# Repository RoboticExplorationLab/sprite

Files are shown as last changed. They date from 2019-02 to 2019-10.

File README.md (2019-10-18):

[hardware](https://github.com/maholli/sprite/tree/master/hardware): KiCad PCB files and bill of materials. Assembling a sprite? Check out [https://roboticexplorationlab.github.io/sprite/](https://roboticexplorationlab.github.io/sprite/) for an interactive BOM!

[firmware](https://github.com/maholli/sprite/tree/master/firmware): pre-built circuitpython bootloader.bin and firmware.uf2 (and the files to build it yourself)

[software](https://github.com/maholli/sprite/tree/master/software): circuitpython scripts and libraries working on the sprite

<br>
<br>
<br>

----

<p align="middle">
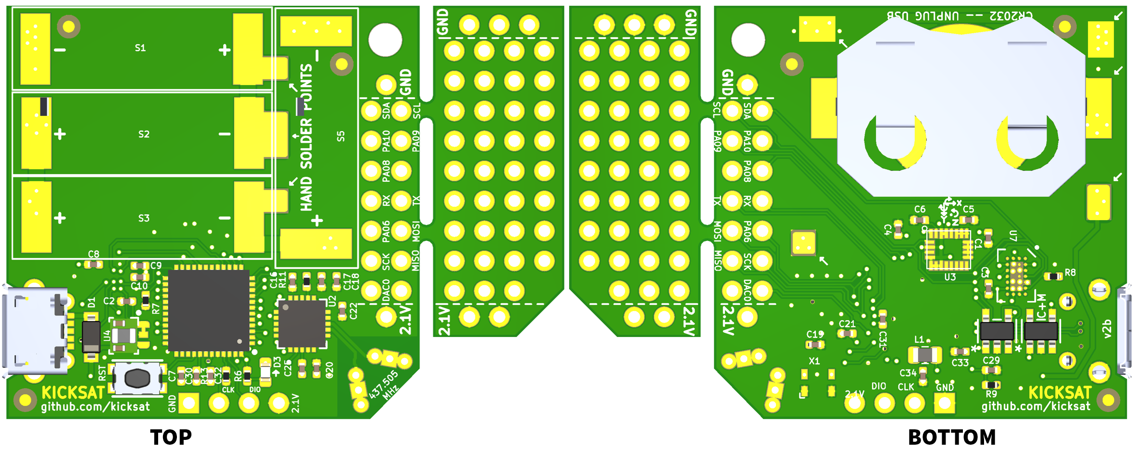
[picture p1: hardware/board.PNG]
  
</p>

### 💡 Lots of applicable information also located on the [PyCubed.org quickstart page](https://www.notion.so/maholli/Hands-On-Quick-Start-d220f0ec88eb41c08ee855ff4f46d737).

## Demos

Put all the files located in [/software/](/software/) on to the sprite and start the serial console (as described above). After pressing <kbd>Ctrl</kbd>+<kbd>C</kbd> to halt the sprite, press any key to enter the REPL, then type

```
import NAMEOFFILE
```

and press enter to execute the example. For example, it we wanted to run blink.py, it would be...

```
import blink
```

1. blink.py - will blink the green LED. 
2. i2c_IMU.py - samples all available sensors on the IMU and prints the results
3. cursor.py - uses the X,Y data from the IMU accelerometer and moves the computer cursor accordingly
4. cpc_test.py - example transmit message for the CC1101 radio

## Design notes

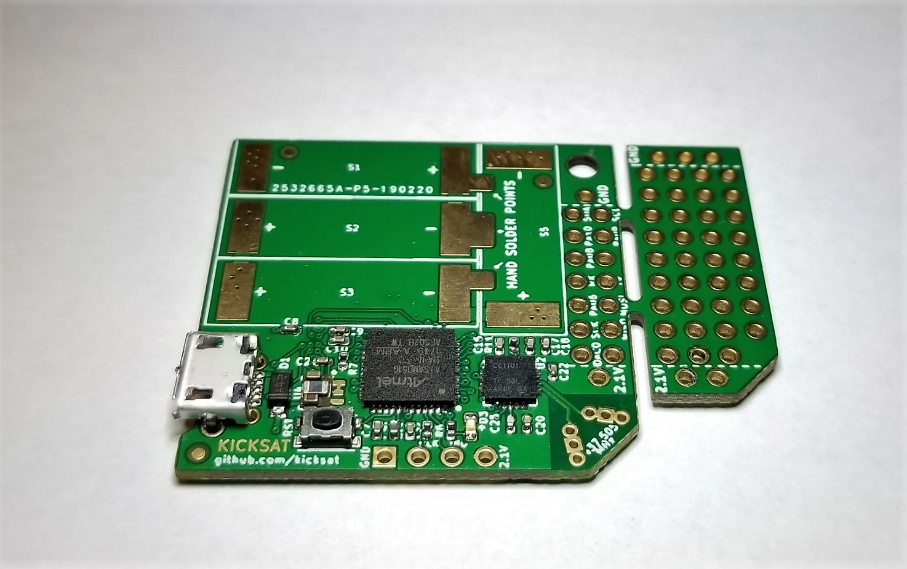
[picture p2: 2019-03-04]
hardware/sprite_top.jpg

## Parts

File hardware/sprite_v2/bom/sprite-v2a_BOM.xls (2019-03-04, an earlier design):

BOM: sprite-v2a
Assembly Part Number/Revision: v2a
Customer / Company Name: Max Holliday, Stanford University
Item # | Quantity per board | Manufacturer Part # | Do Not Install | Reference designators | Vendor (optional) | Vendor Part Number (optional) | Value (optional) | Size / Footprint (optional) | Part description/ specs (optional, but recommended) | Manfacturer (optional)
2 | 1 | 7L2609LCSC-CGG4S |  | X1 |  |  | 26.000 |  | TXCO_2.5x2
3 | 1 | CC1101RGPR |  | U2 |  |  | CC1101RGPR |  | CC1101_RGP_20
4 | 1 | OVM9724 | DNI | U7 |  |  | OVM9724 |  | OVM9724b
5 | 1 | BAT-HLD-001 | DNI | U1 |  |  | BAT-HLD-001 |  | BAT-HLD-001
10 | 1 | 10118194-0001LF |  | J1 |  |  | 10118194-0001LF |  | 10118194-0001LF
11 | 1 | CMI201209X100KT |  | L1 |  |  | 10uH |  | L_0805_2012Metric
12 | 4 | CL05B105KQ5NQNC |  | C7,C29,C33,C31 |  |  | 1uF |  | C_0402_1005Metric
14 | 1 | SOD4004-SH |  | D1 |  |  | MBR120 |  | D_SOD-123
15 | 1 | TJ-S1608SW6TGLC2G-A5 |  | D3 |  |  | GREEN LED |  | LED_0603_1608Metric
16 | 4 | KXOB22-04X3F | DNI | S3,S5,S1,S2 |  |  | KXOB22-04X3F |  | KXOB22-12X1F
17 | 1 | TPS82740ASIP |  | U4 |  |  | TPS82740ASIP |  | TPS82740ASIPR
18 | 4 | RTT021002FTH |  | R8,R9,R13,R7 |  |  | 10K |  | R_0402_1005Metric
19 | 1 | ATSAMD51G_TQFN48 |  | U6 |  |  | ATSAMD51G_TQFN48 |  | QFN50P700X700X90-49N-D
21 | 3 | 0402X106M6R3NT |  | C30,C34,C1 |  |  | 10uF |  | C_0402_1005Metric
22 | 10 | CL05B104KO5NNNC |  | C32,C10,C9,C8,C3,C2,C6,C4,C22,C21 |  |  | 0.1uF |  | C_0402_1005Metric
23 | 2 | DS90LV012ATMFX/NOPB | DNI | U9,U8 |  |  | DS90LV012ATMFX_NOPB |  | DS90
25 | 1 | KMR631NGULCLFS |  | SW2 |  |  | KMR231NG LFS |  | BTN_KMR2_4.6X2.8
26 | 1 | RC0402FR-0756KL |  | R11 |  |  | 56K |  | R_0402_1005Metric
27 | 1 | RC0402FR-07330RL |  | R6 |  |  | 330 |  | R_0402_1005Metric
28 | 4 | CC0402JRX7R9BB103 |  | C25,C20,C18,C5 |  |  | 10nF |  | C_0402_1005Metric
30 | 3 | 0402B221K500NT |  | C19,C17,C16 |  |  | 220pF |  | C_0402_1005Metric
31 | 1 | LSM9DS1TR |  | U3 |  |  | LSM9DS1 |  | LGA24-8X4
END OF BOM

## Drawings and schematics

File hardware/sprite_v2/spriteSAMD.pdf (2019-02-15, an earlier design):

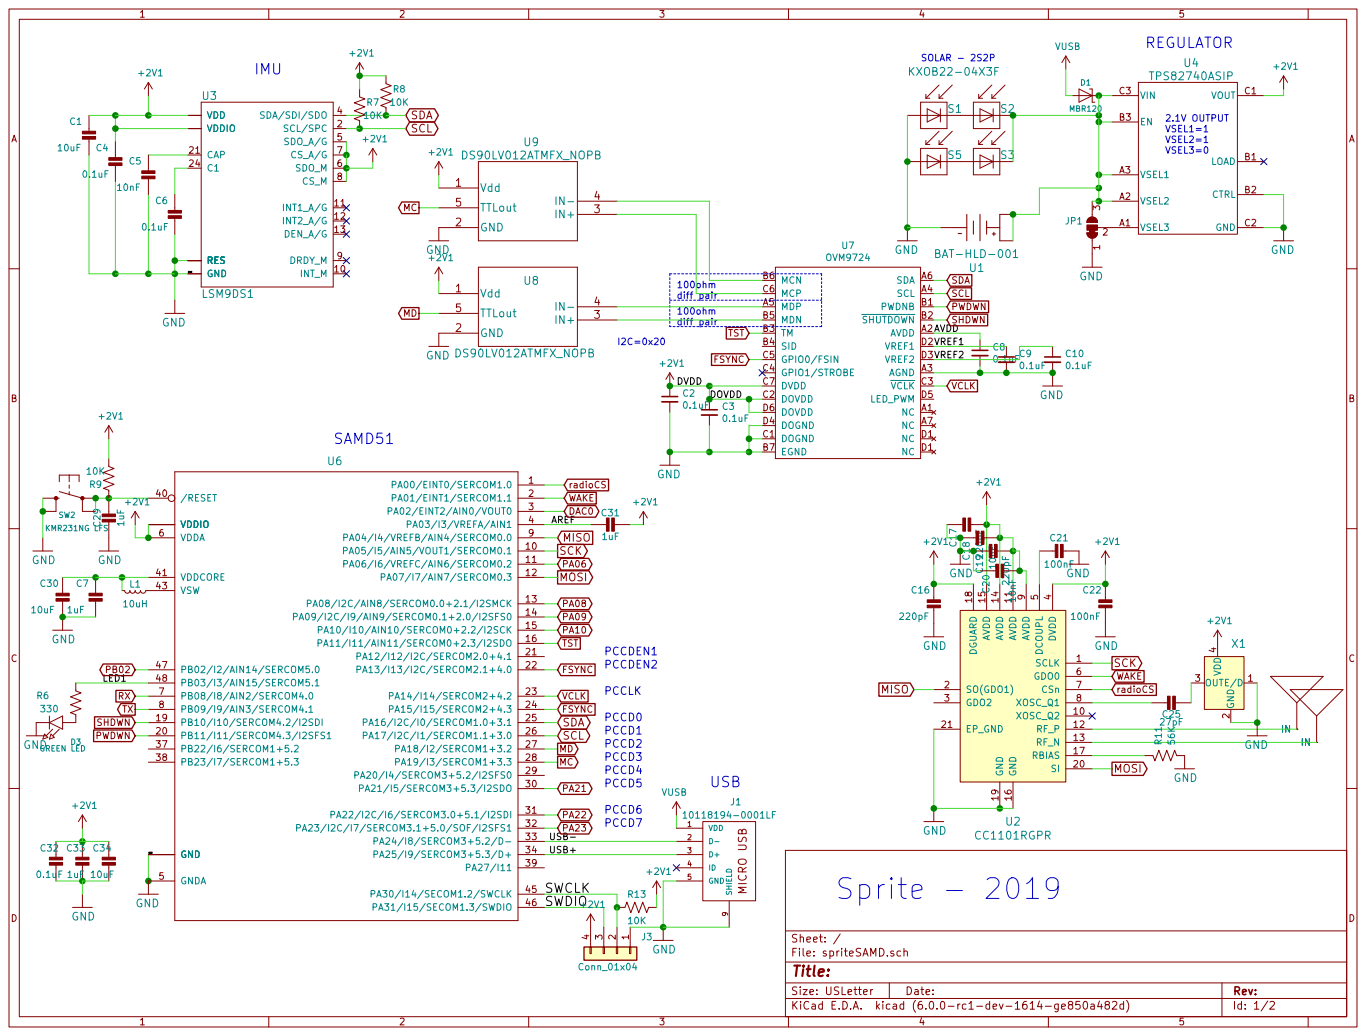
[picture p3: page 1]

9 XOSC_Q2 10 SI 20 AVDD 11 EP_GND 21 RF_P 12 RF_N 13 AVDD 14 AVDD 15 GND 16 RBIAS 17 DGUARD 18 GND 19 U2 CC1101RGPR MOSI MISO

File: spriteSAMD.sch Sheet: /

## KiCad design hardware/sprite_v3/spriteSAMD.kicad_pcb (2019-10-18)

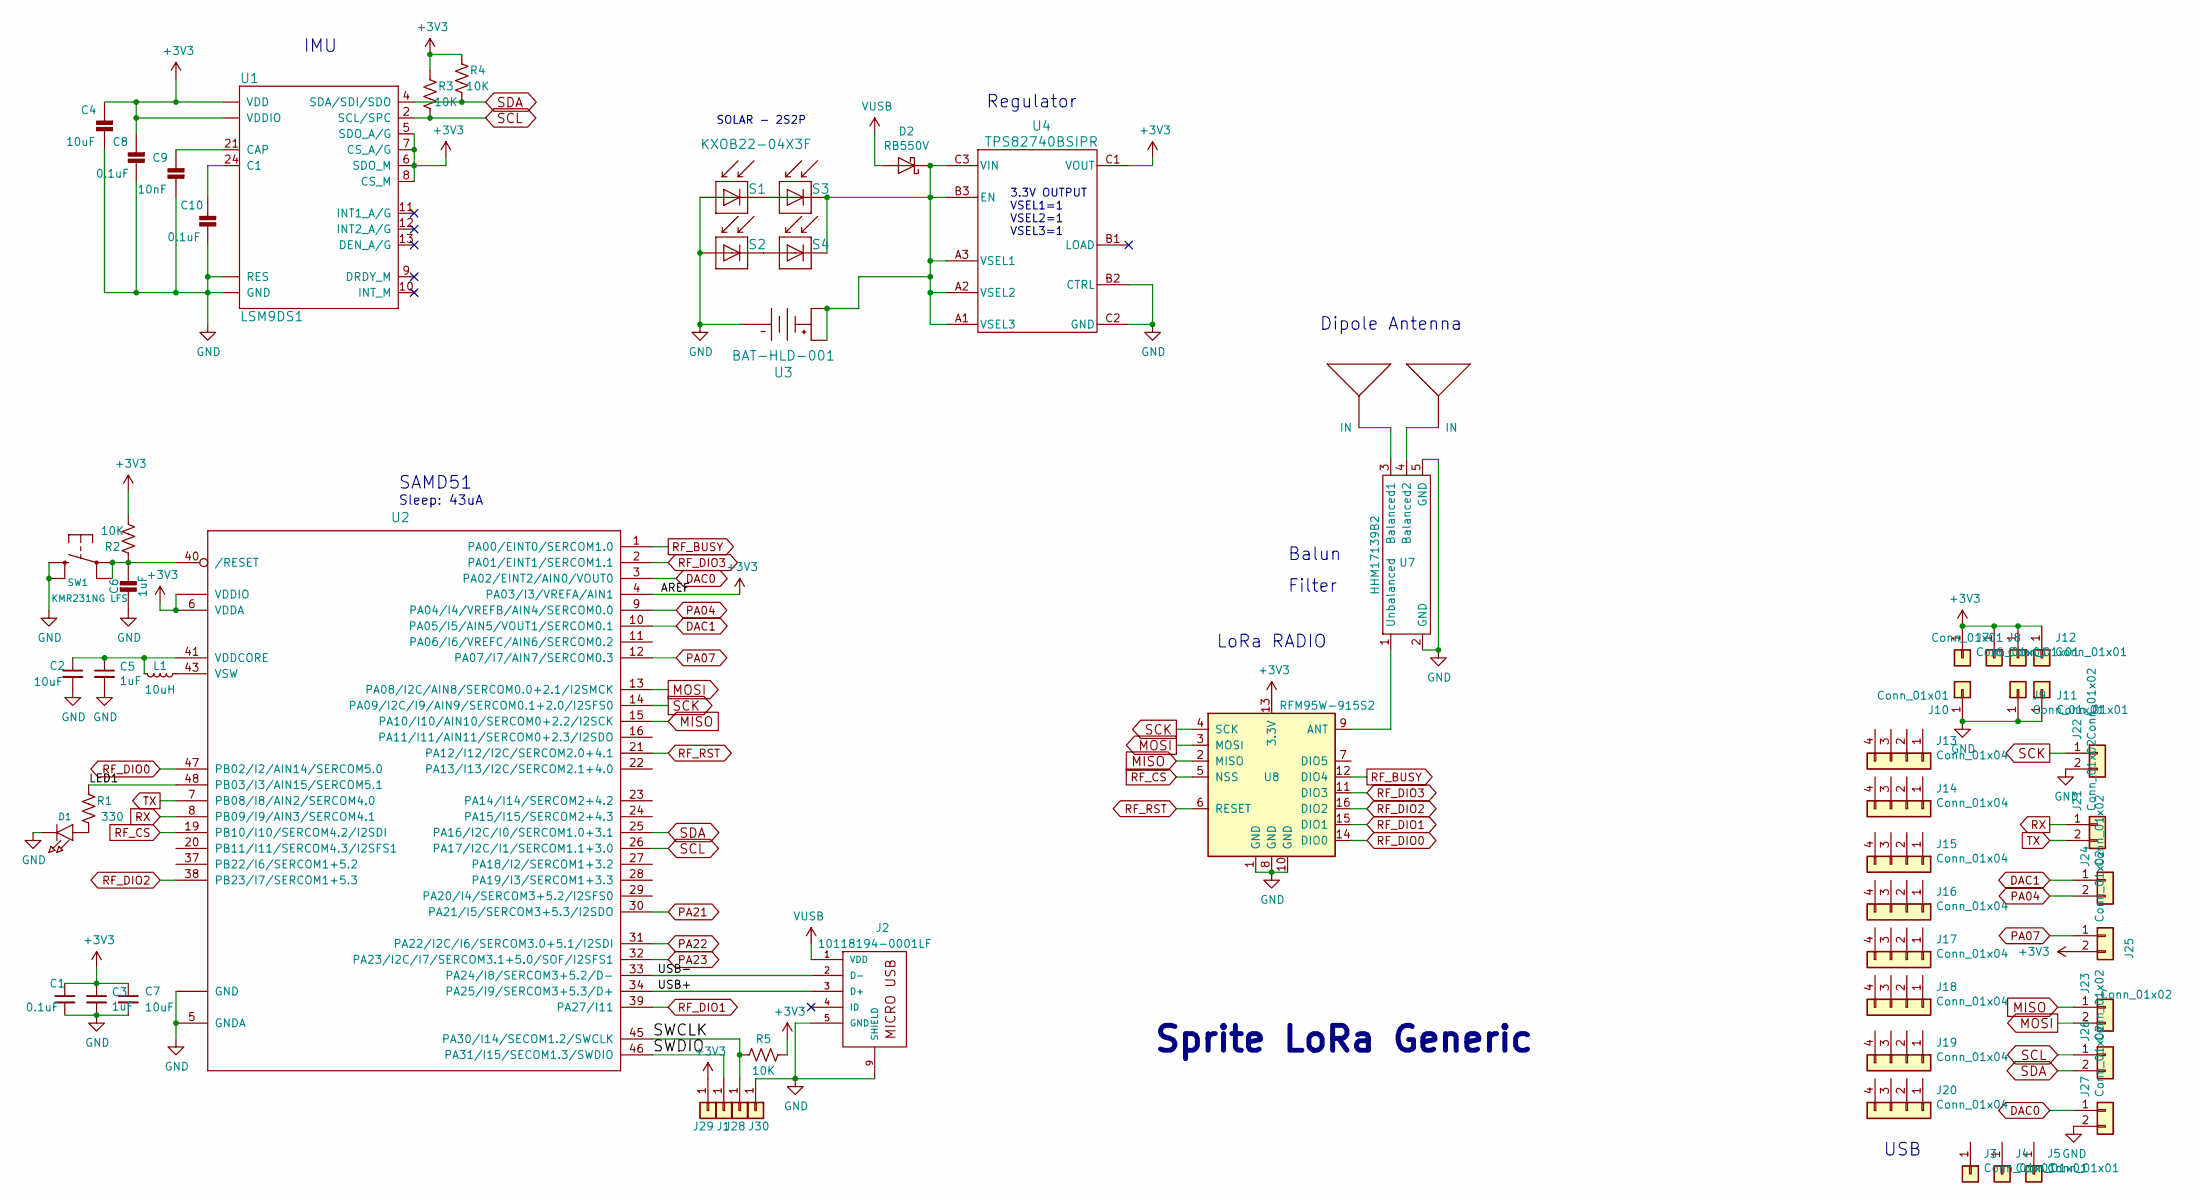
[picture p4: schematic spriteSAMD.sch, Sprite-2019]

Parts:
ANT1, ANT2: ANTENNA
C1, C8, C10: 0.1uF; C_0402_1005Metric
C2, C4, C7: 10uF; C_0402_1005Metric
C3, C5, C6: 1uF; C_0402_1005Metric
C9: 10nF; C_0402_1005Metric
D1: GREEN; LED_0603_1608Metric
D2: RB550V; D_SOD-323
J1, J28, J29, J30: Conn_01x01; castellated_small_1side
J2: 10118194-0001LF
J3, J4, J5, J6, J7, J8, J9, J10, J11, J12: Conn_01x01; PinHeader_CUSTOM2
J13, J14, J15, J16, J17, J18, J19, J20: Conn_01x04; PinHeader_CUSTOM
J21, J22, J23, J24, J25, J26, J27: Conn_01x02; PinHeader_CUSTOM3
L1: 10uH; L_0805_2012Metric
R1: 330; R_0402_1005Metric
R2, R3, R4, R5: 10K; R_0402_1005Metric
S1, S2, S3, S4: KXOB22-04X3F; KXOB22-12X1F
SW1: KMR231NG LFS; BTN_KMR2_4.6X2.8
U1: LSM9DS1; LGA24-8X4
U2: ATSAMD51G_TQFN48; QFN50P700X700X90-49N-D
U3: BAT-HLD-001
U4: TPS82740BSIPR; TPS82740ASIPR
U7: HHM17139B2; balun0603
U8: RFM95W-915S2; HOPERF_RFM9XW_SMD

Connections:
+3V3: C1.1, C3.1, C4.2, C7.1, C8.2, J6.1, J7.1, J8.1, J12.1, J25.2, J29.1, R2.2, R3.1, R4.1, R5.1, U1.1 (VDDIO), U1.3 (VDDIO), U1.5 (SDO_A/G), U1.6 (SDO_M), U1.7 (CS_A/G), U1.8 (CS_M), U1.22 (VDD), U1.23 (VDD), U2.4 (PA03/I3/VREFA/AIN1), U2.6 (VDDA), U2.17 (VDDIO), U2.36 (VDDIO), U2.44 (VDDIO), U4.C1 (VOUT), U8.13 (3.3V)
/LED1: R1.2, U2.48 (PB03/I3/AIN15/SERCOM5.1)
/SWCLK: J28.1, R5.2, U2.45 (PA30/I14/SECOM1.2/SWCLK)
/SWDIO: J1.1, U2.46 (PA31/I15/SECOM1.3/SWDIO)
/USB+: J2.3 (D+), U2.34 (PA25/I9/SERCOM3+5.3/D+)
/USB-: J2.2 (D-), U2.33 (PA24/I8/SERCOM3+5.2/D-)
DAC0: J27.1, U2.3 (PA02/EINT2/AIN0/VOUT0)
DAC1: J24.1, U2.10 (PA05/I5/AIN5/VOUT1/SERCOM0.1)
GND: C1.2, C2.2, C3.2, C4.1, C5.2, C6.1, C7.2, C8.1, C9.1, C10.1, D1.2, J2.5 (GND), J2.8, J2.9 (SHIELD), J9.1, J10.1, J11.1, J22.2, J27.2, J30.1, S1.2, S2.2, SW1.B (S), SW1.B' (S1), U1.14 (RES), U1.15 (RES), U1.16 (RES), U1.17 (RES), U1.18 (RES), U1.19 (GND), U1.20 (GND), U2.5 (GNDA), U2.18 (GND), U2.35 (GND), U2.42 (GND), U2.49, U3.2, U4.B2 (CTRL), U4.C2 (GND), U7.2 (GND), U7.5 (GND), U7.6 (NC), U8.1 (GND), U8.8 (GND), U8.10 (GND)
MISO: J23.1, U2.15 (PA10/I10/AIN10/SERCOM0+2.2/I2SCK), U8.2 (MISO)
MOSI: J23.2, U2.13 (PA08/I2C/AIN8/SERCOM0.0+2.1/I2SMCK), U8.3 (MOSI)
unnamed: ANT1.IN1, ANT1.IN2, ANT1.IN3, U7.3 (Balanced1)
unnamed: ANT2.IN1, ANT2.IN2, ANT2.IN3, U7.4 (Balanced2)
unnamed: C2.1, C5.1, L1.2, U2.41 (VDDCORE)
unnamed: C6.2, R2.1, SW1.A, SW1.A' (P1), U2.40 (/RESET)
unnamed: C9.2, U1.21 (CAP)
unnamed: C10.2, U1.24 (C1)
unnamed: D1.1, R1.1
unnamed: D2.1 (K), S3.1, S4.1, U3.1, U3.3, U4.A1 (VSEL3), U4.A2 (VSEL2), U4.A3 (VSEL1), U4.B3 (EN), U4.C3 (VIN)
unnamed: L1.1, U2.43 (VSW)
unnamed: S1.1, S3.2
unnamed: S2.1, S4.2
unnamed: U7.1 (Unbalanced), U8.9 (ANT)
PA04: J24.2, U2.9 (PA04/I4/VREFB/AIN4/SERCOM0.0)
PA07: J25.1, U2.12 (PA07/I7/AIN7/SERCOM0.3)
PA21: U2.30 (PA21/I5/SERCOM3+5.3/I2SDO)
PA22: U2.31 (PA22/I2C/I6/SERCOM3.0+5.1/I2SDI)
PA23: U2.32 (PA23/I2C/I7/SERCOM3.1+5.0/SOF/I2SFS1)
RF_BUSY: U2.1 (PA00/EINT0/SERCOM1.0), U8.12 (DIO4)
RF_CS: U2.19 (PB10/I10/SERCOM4.2/I2SDI), U8.5 (NSS)
RF_DIO0: U2.47 (PB02/I2/AIN14/SERCOM5.0), U8.14 (DIO0)
RF_DIO1: U2.39 (PA27/I11), U8.15 (DIO1)
RF_DIO2: U2.38 (PB23/I7/SERCOM1+5.3), U8.16 (DIO2)
RF_DIO3: U2.2 (PA01/EINT1/SERCOM1.1), U8.11 (DIO3)
RF_RST: U2.21 (PA12/I12/I2C/SERCOM2.0+4.1), U8.6 (RESET)
RX: J21.1, U2.8 (PB09/I9/AIN3/SERCOM4.1)
SCK: J22.1, U2.14 (PA09/I2C/I9/AIN9/SERCOM0.1+2.0/I2SFS0), U8.4 (SCK)
SCL: J26.1, R3.2, U1.2 (SCL/SPC), U2.26 (PA17/I2C/I1/SERCOM1.1+3.0)
SDA: J26.2, R4.2, U1.4 (SDA/SDI/SDO), U2.25 (PA16/I2C/I0/SERCOM1.0+3.1)
TX: J21.2, U2.7 (PB08/I8/AIN2/SERCOM4.0)
VUSB: D2.2 (A), J2.1 (VDD)

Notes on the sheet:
Regulator
USB
IMU
3.3V OUTPUT VSEL1=1 VSEL2=1 VSEL3=1
SOLAR - 2S2P
SAMD51
LoRa RADIO
Sleep: 43uA
Balun
Filter
Dipole Antenna
Sprite LoRa Generic

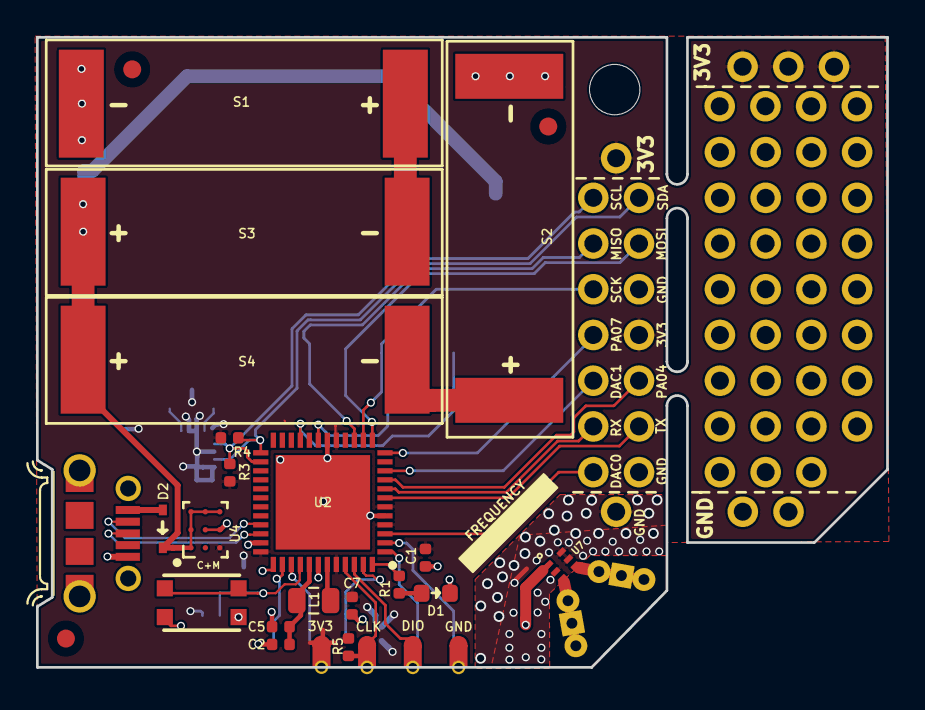
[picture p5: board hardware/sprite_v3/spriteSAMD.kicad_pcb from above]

Board: 2 copper layers, 47.2 x 35.0 mm, 62 parts (0 on the bottom side), 38 nets.

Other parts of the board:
@HOLE0: (no value)

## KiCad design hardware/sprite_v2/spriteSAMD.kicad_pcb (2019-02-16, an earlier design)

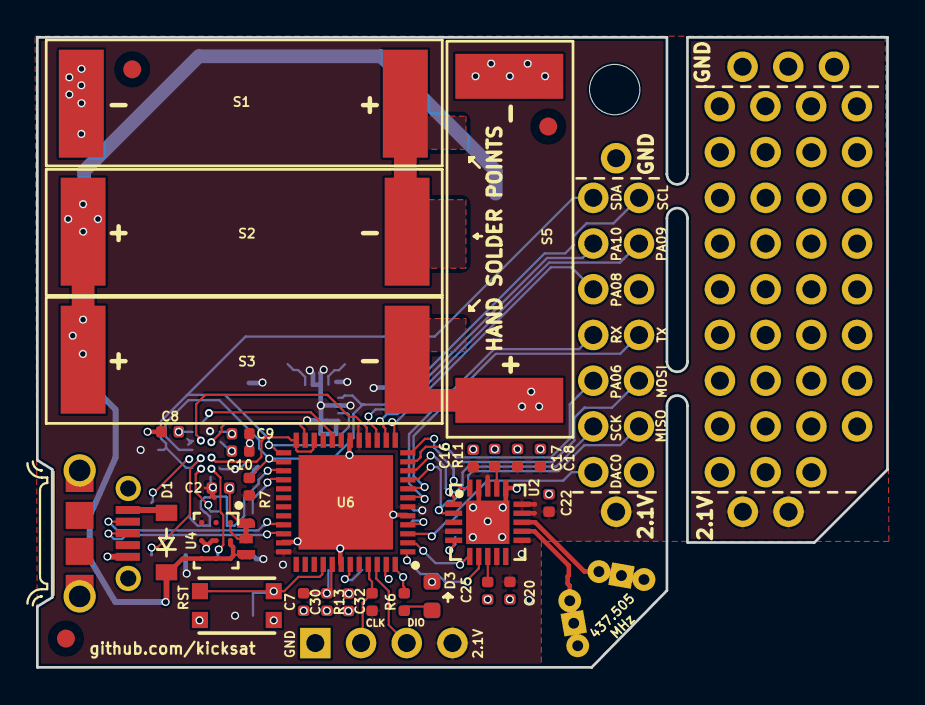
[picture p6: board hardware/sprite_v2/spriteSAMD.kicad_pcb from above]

Board: 2 copper layers, 47.2 x 35.0 mm, 78 parts (0 on the bottom side), 53 nets.

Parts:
@HOLE0: (no value)
ANT-N1: ANTENNA
ANT-P1: ANTENNA
C1, C30, C34: 10uF; C_0402_1005Metric
C2, C3, C4, C6, C8, C9, C10, C32: 0.1uF; C_0402_1005Metric
C5, C18, C20: 10nF; C_0402_1005Metric
C7, C29, C31, C33: 1uF; C_0402_1005Metric
C16, C17, C19: 220pF; C_0402_1005Metric
C21, C22: 100nF; C_0402_1005Metric
C25: 27pF; C_0402_1005Metric
D1: MBR120; D_SOD-123
D3: GREEN LED; LED_0603_1608Metric
J1: 10118194-0001LF
J2, J4, J5, J6, J7, J8, J9, J10, J11, J12: Conn_01x01; PinHeader_CUSTOM2
J3: Conn_01x04; PinHeader_1x04_P2.54mm_Vertical
J13, J14, J15, J16, J17, J18, J19, J20: Conn_01x04; PinHeader_CUSTOM
J21, J22, J23, J24, J25, J26, J27: Conn_01x02; PinHeader_CUSTOM3
JP1: SolderJumper_3_Bridged12; Jumper3_Small
L1: 10uH; L_0805_2012Metric
R6: 330; R_0402_1005Metric
R7, R8, R9, R13: 10K; R_0402_1005Metric
R11: 56K; R_0402_1005Metric
S1, S2, S3, S5: KXOB22-04X3F; KXOB22-12X1F
SW2: KMR231NG LFS; BTN_KMR2_4.6X2.8
U1: BAT-HLD-001
U2: CC1101RGPR; CC1101_RGP_20
U3: LSM9DS1; LGA24-8X4
U4: TPS82740ASIP; TPS82740ASIPR
U6: ATSAMD51G_TQFN48; QFN50P700X700X90-49N-D
U7: OVM9724; OVM9724b
U8, U9: DS90LV012ATMFX_NOPB; DS90
X1: 26.000; TXCO_2.5x2

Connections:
+2V1: C1.2, C2.1, C3.1, C4.2, C16.2, C17.1, C18.1, C19.1, C20.1, C22.2, C31.2, C32.1, C33.1, C34.1, J3.4, J6.1, J9.1, J11.1, R7.1, R8.1, R9.2, R13.1, U2.4, U2.9, U2.11, U2.14, U2.15, U2.18, U3.1, U3.3, U3.5, U3.6, U3.7, U3.8, U3.22, U3.23, U4.C1, U6.6, U6.17, U6.36, U6.44, U7.C2, U7.C7, U7.D6, U8.1, U9.1, X1.4
/AREF: C31.1, U6.4
/AVDD: C8.1, U7.A2
/LED1: R6.2, U6.48
/SWCLK: J3.2, R13.2, U6.45
/SWDIO: J3.3, U6.46
/USB+: J1.3, U6.34
/USB-: J1.2, U6.33
/VREF1: C9.1, U7.D2
/VREF2: C10.1, U7.D3
DAC0: J27.1, U6.3
FSYNC: U6.22, U6.24, U7.C5
GND: C1.1, C2.2, C3.2, C4.1, C5.1, C6.1, C7.1, C8.2, C9.2, C10.2, C16.1, C17.2, C18.2, C19.2, C20.2, C21.2, C22.1, C29.1, C30.1, C32.2, C33.2, C34.2, D3.2, J1.5, J1.8, J1.9, J3.1, J7.1, J8.1, J10.1, J12.1, JP1.1, R11.2, S1.2, S5.2, SW2.B, SW2.B', U1.2, U2.16, U2.19, U2.21, U3.14, U3.15, U3.16, U3.17, U3.18, U3.19, U3.20, U4.B2, U4.C2, U6.5, U6.18, U6.35, U6.42, U6.49, U7.A3, U7.B7, U7.C1, U7.D4, U8.2, U9.2, X1.1, X1.2
MC: U6.28, U9.5
MD: U6.27, U8.5
MISO: J21.2, U2.2, U6.9
MOSI: J24.2, U2.20, U6.12
unnamed: ANT-N1.IN1, ANT-N1.IN2, ANT-N1.IN3, U2.13
unnamed: ANT-P1.IN1, ANT-P1.IN2, ANT-P1.IN3, U2.12
unnamed: C5.2, U3.21
unnamed: C6.2, U3.24
unnamed: C21.1, U2.5
unnamed: C25.1, U2.8
unnamed: C25.2, X1.3
unnamed: C29.2, R9.1, SW2.A, SW2.A', U6.40
unnamed: C7.2, C30.2, L1.2, U6.41
unnamed: D1.1, JP1.3, S2.1, S3.1, U1.1, U1.3, U4.A2, U4.A3, U4.B3, U4.C3
unnamed: D3.1, R6.1
unnamed: JP1.2, U4.A1
unnamed: L1.1, U6.43
unnamed: R11.1, U2.17
unnamed: S1.1, S2.2
unnamed: S3.2, S5.1
unnamed: U7.A5, U8.4
unnamed: U7.B5, U8.3
unnamed: U7.B6, U9.4
unnamed: U7.C6, U9.3
PA06: J24.1, U6.11
PA08: J22.1, U6.13
PA09: J23.2, U6.14
PA10: J23.1, U6.15
PWDWN: U6.20, U7.B1
RX: J25.1, U6.7
SCK: J21.1, U2.1, U6.10
SCL: J26.2, R7.2, U3.2, U6.26, U7.A4
SDA: J26.1, R8.2, U3.4, U6.25, U7.A6
SHDWN: U6.19, U7.B2
TST: U6.16, U7.B3
TX: J25.2, U6.8
VCLK: U6.23, U7.C3
VUSB: D1.2, J1.1
WAKE: U2.6, U6.2
radioCS: U2.7, U6.1

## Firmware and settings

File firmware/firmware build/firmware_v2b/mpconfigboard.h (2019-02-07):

#define MICROPY_HW_BOARD_NAME "sprite v2a"
#define MICROPY_HW_MCU_NAME "samd51G19"
#define CIRCUITPY_MCU_FAMILY samd51

#define MICROPY_HW_LED_STATUS   (&pin_PB03)

#define MICROPY_PORT_A        (PORT_PA24 | PORT_PA25)
#define MICROPY_PORT_B        (0)
#define MICROPY_PORT_C        (0)
#define MICROPY_PORT_D 		  (0)

#define CALIBRATE_CRYSTALLESS 1

#define CIRCUITPY_INTERNAL_NVM_SIZE 0

#define BOARD_FLASH_SIZE (FLASH_SIZE - 0x4000 - 0x010000)

#define DEFAULT_I2C_BUS_SCL  (&pin_PA17)
#define DEFAULT_I2C_BUS_SDA  (&pin_PA16)

#define DEFAULT_SPI_BUS_SCK  (&pin_PA05)
#define DEFAULT_SPI_BUS_MOSI (&pin_PA07)
#define DEFAULT_SPI_BUS_MISO (&pin_PA04)

#define DEFAULT_UART_BUS_TX  (&pin_PB09)
#define DEFAULT_UART_BUS_RX  (&pin_PB08)

#define IGNORE_PIN_PA24     1
#define IGNORE_PIN_PA25     1

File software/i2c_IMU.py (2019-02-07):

import time
import board
import busio
import adafruit_lsm9ds1

# I2C connection:
i2c = busio.I2C(board.SCL, board.SDA)
sensor = adafruit_lsm9ds1.LSM9DS1_I2C(i2c)


#### ONLY GYRO/

while True:
    # Read acceleration, magnetometer, gyroscope, temperature.
    accel_x, accel_y, accel_z = sensor.acceleration
    mag_x, mag_y, mag_z = sensor.magnetic
    gyro_x, gyro_y, gyro_z = sensor.gyro
    temp = sensor.temperature
    # Print values.
    print('Acceleration (m/s^2): ({0:0.3f},{1:0.3f},{2:0.3f})'.format(accel_x, accel_y, accel_z))
    print('Magnetometer (gauss): ({0:0.3f},{1:0.3f},{2:0.3f})'.format(mag_x, mag_y, mag_z))
    print('Gyroscope (degrees/sec): ({0:0.3f},{1:0.3f},{2:0.3f})'.format(gyro_x, gyro_y, gyro_z))
    print('Temperature: {0:0.3f}C'.format(temp))
    
    # Delay for a second.
    time.sleep(1.0)

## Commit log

2019-02-07 initial commit of v2a will need to update hardware to v2b
    [Digikey_2019-01-17.xlsx, LCSC_Exported_20190118_094724.xlsx, spriteSAMD.kicad_pcb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]
2019-02-07 adding interactive BOM
2019-02-15 updating to v2b (TXCO added)
    [sprite-v2a_BOM.xls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]
2019-02-15 Via drills changed 0.25 to 0.3 mm
    [LCSC_Exported_20190213_002853.xlsx, sprite-v2a_BOM.xls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]
2019-02-16 silly fixes for fab house
    [spriteSAMD-B_Mask.gbr, spriteSAMD-B_Paste.gbr, spriteSAMD-B_SilkS.gbr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]
2019-03-03 new board image
2019-10-18 finally adding modular radio version + repo cleanup
    [Digikey_2019-01-17.xlsx, LCSC_Exported_20190118_094724.xlsx, LCSC_Exported_20190213_002853.xlsx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]

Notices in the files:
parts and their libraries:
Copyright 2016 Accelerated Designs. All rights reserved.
